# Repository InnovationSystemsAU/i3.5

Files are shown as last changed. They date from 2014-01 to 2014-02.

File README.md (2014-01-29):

i3-ImprovedPP
=============

Prusa i3 Improved ++ For Lasercut

A modified Prusa Iteration 3 printer, designed to have a rigid lasercut frame.

Our modifications include simplification, improvements to the frame, reliability improvements and have optimised the design for next generation
concepts such as direct drive, hall effect sensors and more to come.

Build images can be seen here -

https://imgur.com/a/1nFgI#0

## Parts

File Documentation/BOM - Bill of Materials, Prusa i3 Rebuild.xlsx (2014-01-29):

Revision History
Issue | Release date | Prepared by |  | Reviewed by | Approved by
A |  | M.Croucher
Project Title: | Prusa i3 Improved ++
Notes: | 1. All costs are excluding GST
Line Item | Sub Assembly | Part Number | Issue | Description | Qty/Unit | Supplier | Ordered | Cost per Item | Cost Total
1 | Laser Cut Parts | Prusa_i3_Frame_V2_Laser_Cut_Layout.dxf |  | Frame, Main | 1 |  |  |  | $0.00
2 |  |  |  | Upright, Main Frame | 2 |  |  |  | $0.00
3 |  |  |  | Mount, z-axis Motor | 2 |  |  |  | $0.00
4 |  |  |  | Support, z-axis Motor Mount | 4 |  |  |  | $0.00
5 |  |  |  | Support, z-axis Guide Support | 2 |  |  |  | $0.00
7 | Printed Parts |  |  |  |  |  |  |  | $0.00
8 |  | i3 Improved ++ 1x Y Corner.stl |  | y-Corners | 4 |  |  |  | $0.00
9 |  | i3 Improved ++ X Carriage HD.stl |  | x-Carriage, Heavy Duty | 1 |  |  |  | $0.00
10 |  | i3 Improved ++ X Carriage SD.stl |  | x-Carriage, Standard Duty | 1 |  |  |  | $0.00
11 |  | i3 Improved ++ X Idler End.stl |  | x-axis, Idler End | 1 |  |  |  | $0.00
12 |  | i3 Improved ++ X Motor End.stl |  | x-axis, Motor End | 1 |  |  |  | $0.00
13 |  | i3 Improved ++ Y Belt Clamp.stl |  | y-Carriage, Belt Clamp | 1 |  |  |  | $0.00
14 |  | i3 Improved ++ Y Idler End 8mm.stl |  | y-Carriage, Idler End | 1 |  |  |  | $0.00
15 |  | i3 Improved ++ Y Carriage LM8UU Holder.stl |  | y-Carriage, Bearing Holder | 3 |  |  |  | $0.00
16 |  | i3 Improved ++ Y Motor Mount.stl |  | Mount, y-Motor, w/end stop | 1 |  |  |  | $0.00
17 |  | i3 Logo 30mm Fan Guard.stl |  | Guard, fan 30mm | 1 |  |  |  | $0.00
18 |  | i3 Logo 40mm Fan Guard.stl |  | Guard, fan 40mm | 1 |  |  |  | $0.00
19 |  | 608pulley.stl |  | Pulley, 608 | 2 |  |  |  | $0.00
20 |  | Generic 40mm Fan Mounted LED Strip.stl |  | Strip, Fan Mounted LED strip | 2 |  |  |  | $0.00
21.35087719 |  | i3_improved__x_rod_stabiliser.stl |  | Stabiliser, y-axis Rod | 2 |  |  |  | $0.00
22.4122807 | Direct Drive Extruder |  |  |  |  |  |  |  | $0.00
23.47368421 | Groove Mount | i3 Improved ++ Direct Drive Extruder Mount.stl |  | Mount, Direct Drive Extruder | 1 |  |  |  | $0.00
24.53508772 |  | i3 Improved ++ Direct Drive Extruder Mount.stl |  | Mount, 40mm Fan | 1 |  |  |  | $0.00
25.59649123 |  |  |  |  |  |  |  |  | $0.00
26.65789474 | Budaschnozzle Mount | i3 Improved ++ Buddasch Extruder Mount.stl |  | Mount, Budasch Extruder | 1 |  |  |  | $0.00
27.71929825 |  |  |  |  |  |  |  |  | $0.00
28.78070175 | Ubis Mount |  |  |  |  |  |  |  | $0.00
29.84210526 |  |  |  |  |  |  |  |  | $0.00
30.90350877 |  |  |  |  |  |  |  |  | $0.00
31.96491228 |  |  |  |  |  |  |  |  | $0.00
33.02631579 |  |  |  |  |  |  |  |  | $0.00
34.0877193 | Rod |  |  | Threaded Rod - M8 Stainless Steel, 210mm LG | 3 |  |  |  | $0.00 | M8 Total: | 1790
35.14912281 |  |  |  | Threaded Rod - M8 Stainless Steel, 280mm LG | 1 |  |  |  | $0.00
36.21052632 |  |  |  | Threaded Rod - M8 Stainless Steel, 440mm LG | 2 |  |  |  | $0.00
37.27192982 |  |  |  | Threaded Rod - M5 Stainless Steel 306 300mm LG | 2 |  |  |  | $0.00 | M5 Total: | 600
38.33333333 |  |  |  | Ground Rod, Chrome, Hardened, Æ8mm 405mm LG | 2 |  |  |  | $0.00 | 8mm Rod Total: | 1510
39.39473684 |  |  |  | Ground Rod, Chrome, Hardened, Æ8mm 350mm LG Max | 2 |  |  |  | $0.00
40.45614035 | Fasteners |  |  |  |  |  |  |  | $0.00
41.51754386 | Screws | Motor Screws |  | M3 x 10 LG Socket Head Cap Screw | 15 | Fastener Express (http://www.fastener-express.com/) |  |  | $0.00
42.57894737 |  | Chassis Screws |  | M3 x 15 LG Socket Head Cap Screw | 24 |  |  |  | $0.00
43.64035088 |  |  |  | M3 x 20 LG Socket Head Cap Screw | 8 |  |  |  | $0.00
44.70175439 |  | M4 Tension Screw |  | M4 x 20 LG Socket Head Cap Screw | 1 |  |  |  | $0.00
45.76315789 |  | Pulley Screws |  | M8 x 20 LG Socket Head Cap Screw | 2 |  |  |  | $0.00
46.8245614 | Nuts |  |  | M3 Nut | 18 |  |  |  | $0.00
47.88596491 |  |  |  | M3 Lock Nut | 18 |  |  |  | $0.00
48.94736842 |  | y-belt tension nut |  | M4 Lock Nut | 1 |  |  |  | $0.00
50.00877193 |  | z-axis leadscrew nuts |  | M5 Brass Nut (or Zinc Plate, Not Stainless) | 2 |  |  |  | $0.00
51.07017544 |  |  |  | M8 Nut, Stainless | 22 |  |  |  | $0.00
52.13157895 |  |  |  | M8 Lock Nut, Stainless | 14 |  |  |  | $0.00
53.19298246 | Washers |  |  | M3 Washer | 43 |  |  |  | $0.00
54.25438596 |  |  |  | M8 Washer | 22 |  |  |  | $0.00
55.31578947 | Spring Washers |  |  | M3 Wave/Conical washer | 18 |  |  |  | $0.00
56.37719298 |  |  |  | M8 Spring Washer/Conical washer | 26 |  |  |  | $0.00
57.43859649 | Vitamins |  |  |  |  |  |  |  | $0.00
58.5 |  | Upright Support Brackets |  | Brackets - Bunnings 60x60mm | 2 |  |  |  | $0.00
59.56140351 |  | Y-Belt |  | GT-2 725 LG | 1 | Bilby CNC | Y | $4.00 | $4.00 | Total Ln: | 1570
60.62280702 |  | X-Belt |  | GT-2 845 LG | 1 | Bilby CNC | Y | $4.00 | $4.00
61.68421053 |  | Belt Pulleys |  | GT-2 Pulleys, 16 Teeth, Twin Flange | 2 | Bilby CNC | Y | $5.40 | $10.80
62.74561404 |  |  |  | Bearing, LM8UU Linear (8 for Heavy, 7 for Std) | 8 | Bilby CNC | Y | $1.25 | $10.00
63.80701754 |  |  |  | Bearing, 608Z | 2 | Bilby CNC | Y | $1.50 | $3.00
64.86842105 |  | Extruder |  | Bearing, 624ZZ | 1 | Bilby CNC | Y | $1.20 | $1.20
65.92982456 |  |  |  | Small Cable Ties | 10 |  |  |  | $0.00
66.99122807 |  |  |  | Fan, 40mm, 12VDC | 1 | Bilby CNC | Y | $2.95 | $2.95
68.05263158 |  |  |  | Fan, 30mm, 12VDC | 1 |  |  |  | $0.00
69.11403509 |  |  |  | NEMA 17 Motors | 5 |  |  |  | $0.00
70.1754386 |  |  |  | Coupler, Flexible 5mm to 5mm | 2 | Bilby CNC | Y | $5.45 | $10.90
71.23684211 |  |  |  | Hall Effect Endstop, z-axis | 1 | Bilby CNC | Y | $17.95 | $17.95
72.29824561 |  |  |  | Electronics, |  |  |  |  | $0.00
73.35964912 |  |  |  | Cables |  |  |  |  | $0.00
74.42105263 |  |  |  | LED Strip |  |  |  |  | $0.00
75.48245614 |  |  |  | Build Platform |  |  |  |  | $0.00
76.54385965 |  |  |  | 3D Printing Cream Tape, 48mm wide x 50mm LG | 1 | Bilby CNC | Y | $19.95 | $19.95
77.60526316 | Hot End |  |  |  |  |  |  |  | $0.00
78.66666667 |  |  |  | Brass Barrel, M6 x 40 LG, 1.75 ID | 1 | Bilby CNC | Y | $8.95 | $8.95
79.72807018 |  |  |  | Teflon Tube for Barrel Conversion | 1 | Bilby CNC | Y | $5.45 | $5.45
80.78947368 |  |  |  | Ceramic Insulation Tape | 1 | Bilby CNC | Y | $2.50 | $2.50
81.85087719
82.9122807
83.97368421
85.03508772
86.09649123
87.15789474
88.21929825

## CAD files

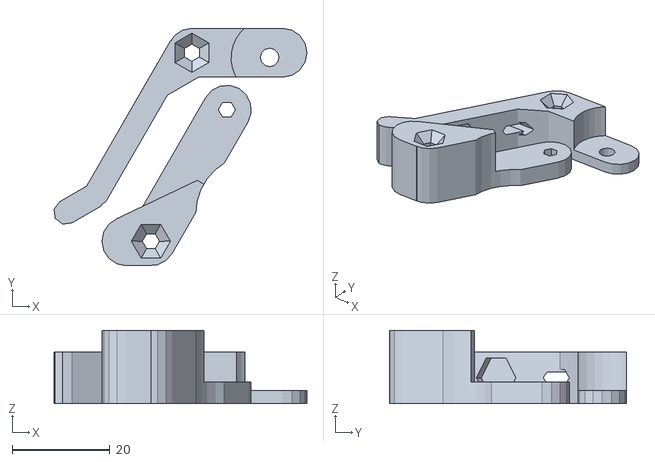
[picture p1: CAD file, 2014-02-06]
i3 Improved ++ Extruder Idler Assembly.stl
51.6 x 48.5 x 15.0

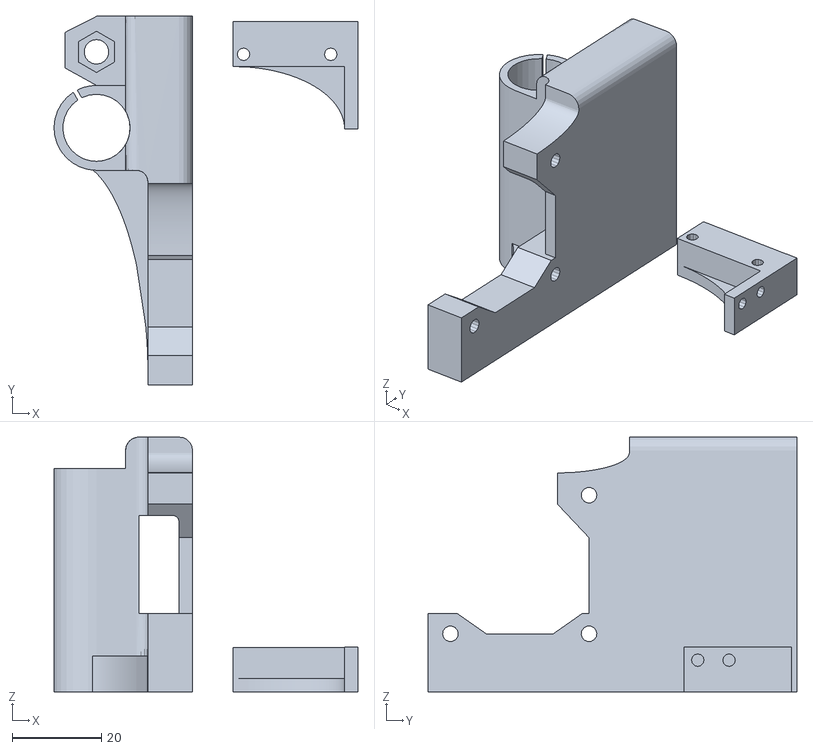
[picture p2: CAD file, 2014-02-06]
i3 Improved ++ X Motor End Assembly.stl
68.0 x 82.5 x 57.0

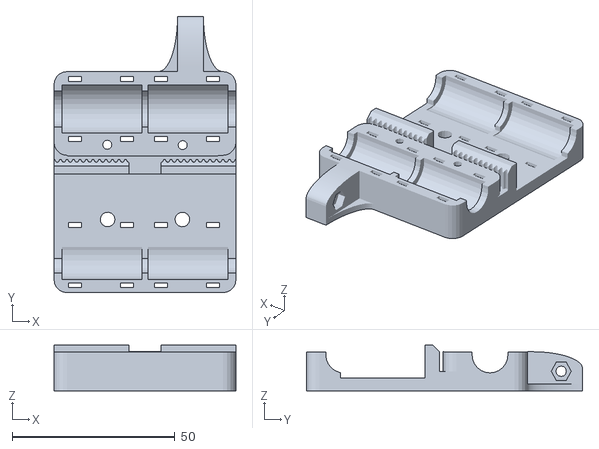
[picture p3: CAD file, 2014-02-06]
i3 Improved ++ X Carriage.stl
56.0 x 85.0 x 14.0

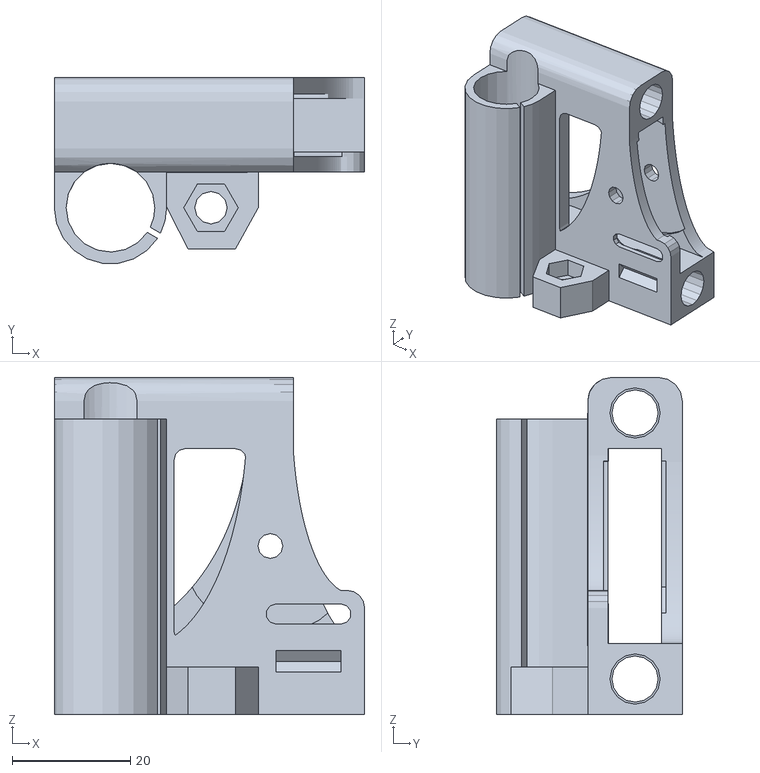
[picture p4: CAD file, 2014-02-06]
i3 Improved ++ X Idler End.stl
52.5 x 31.4 x 57.0

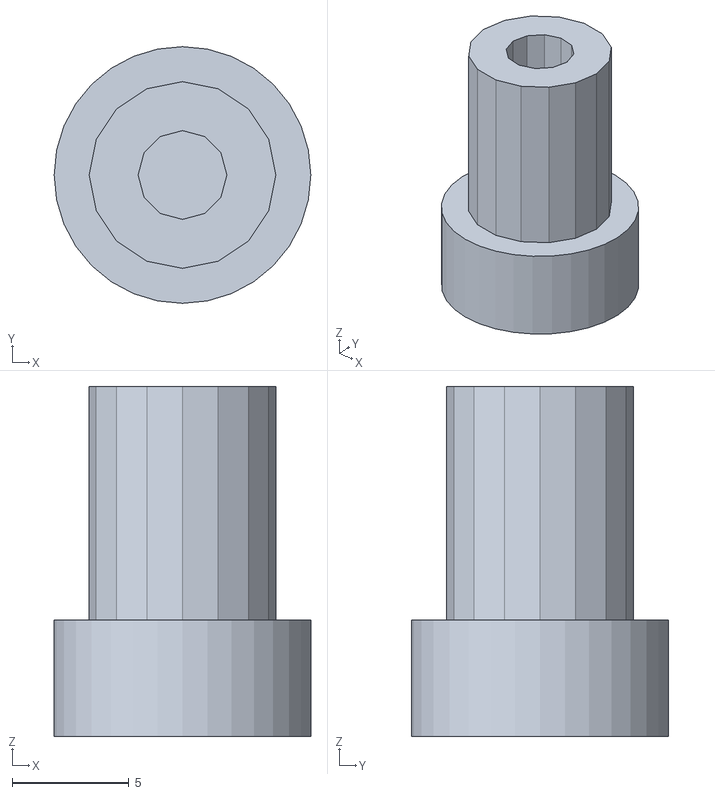
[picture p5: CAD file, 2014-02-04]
i3 Improved ++ Z End Stop Hall Effect Probe.stl
11.0 x 11.0 x 15.0

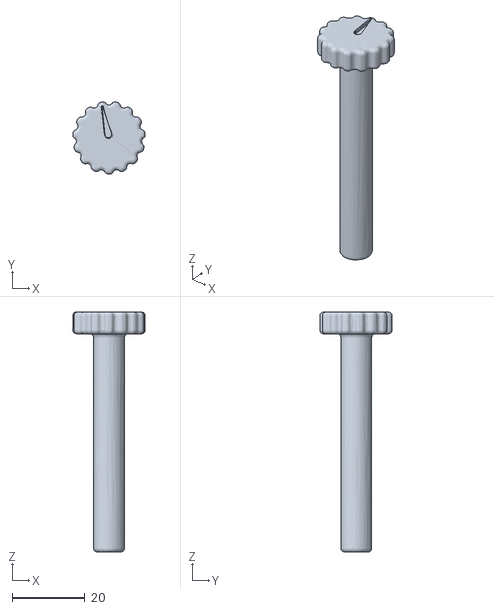
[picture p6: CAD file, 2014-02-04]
i3 Improved ++ Z End Stop Adjustment Dial.stl
19.9 x 19.8 x 66.0

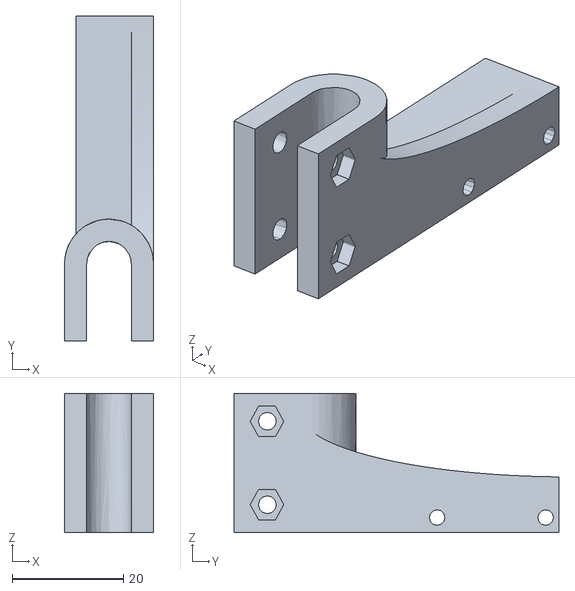
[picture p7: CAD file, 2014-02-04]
i3 Improved ++ Z End Stop Mount.stl
16.0 x 58.4 x 25.0

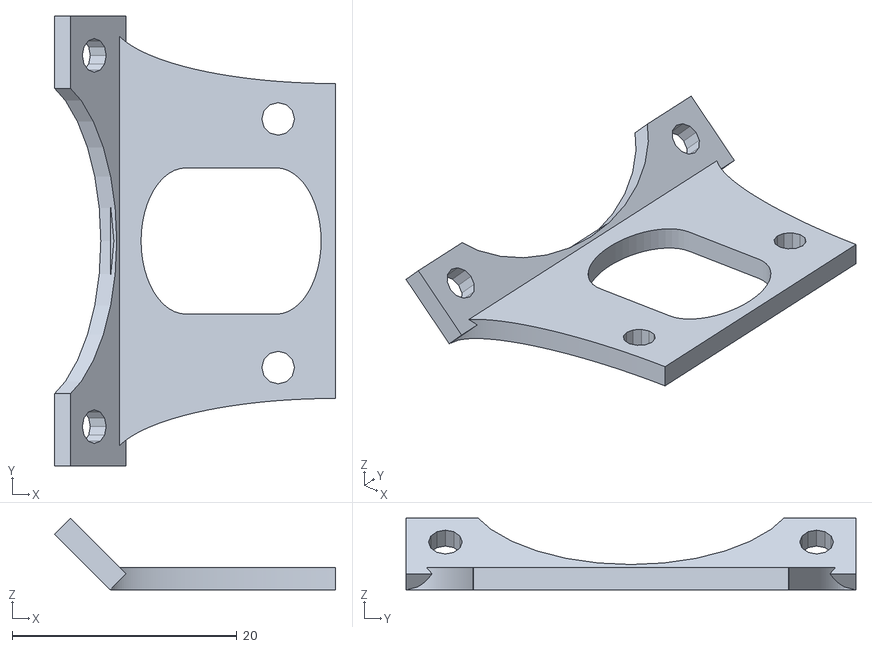
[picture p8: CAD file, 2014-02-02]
i3 Improved ++ Extruder Mount 45 degree Fan Mount.stl
25.0 x 40.0 x 6.36

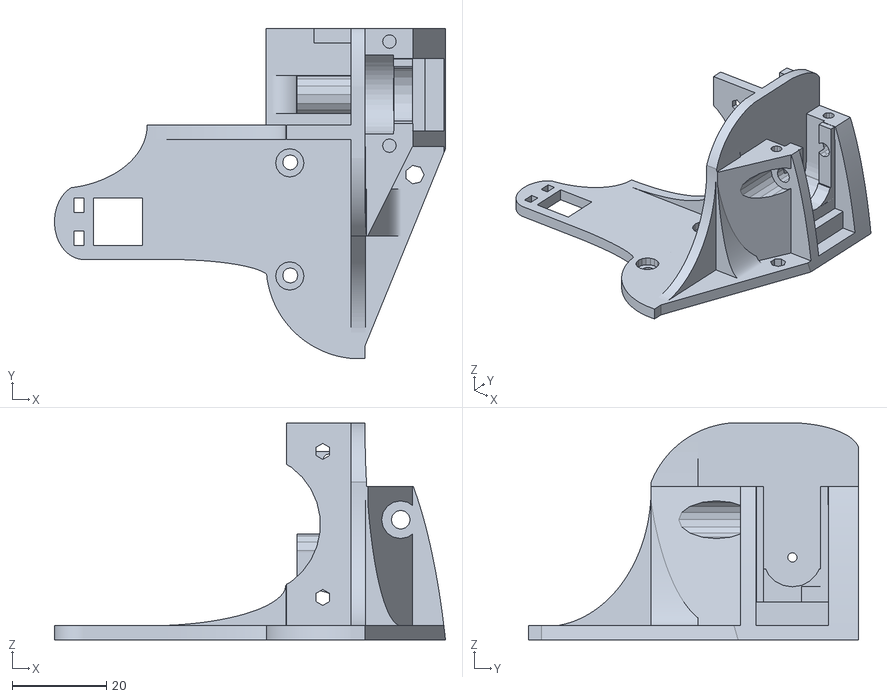
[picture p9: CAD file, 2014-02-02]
i3 Improved ++ Extruder Mount Groove Style.stl
83.0 x 70.0 x 46.0

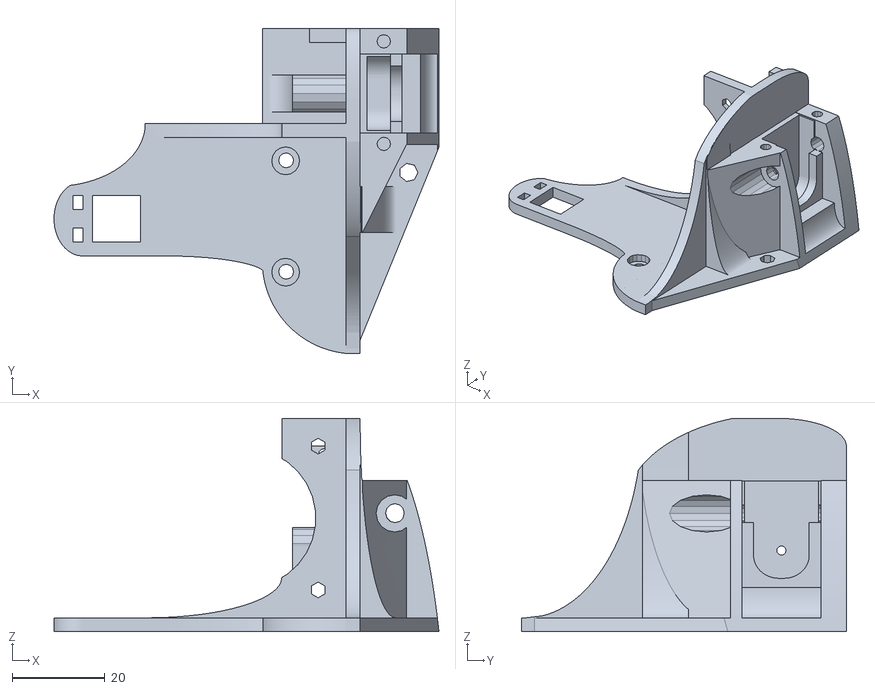
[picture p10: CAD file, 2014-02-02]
i3 Improved ++ Extruder Mount UBIS Style.stl
83.0 x 70.0 x 46.0

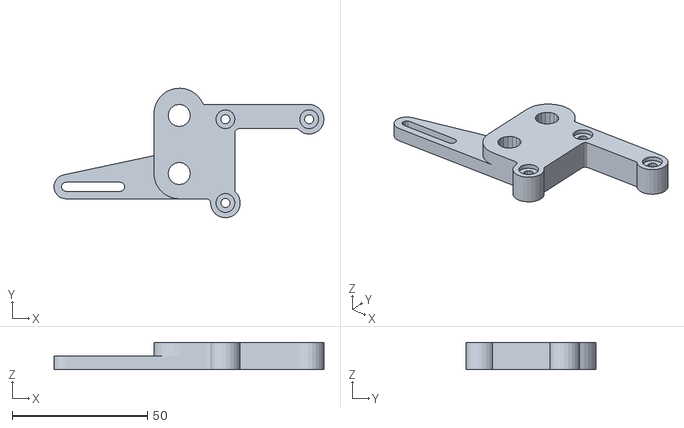
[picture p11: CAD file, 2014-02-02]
i3 Improved ++ Y Motor Mount.stl
100.0 x 48.0 x 10.0

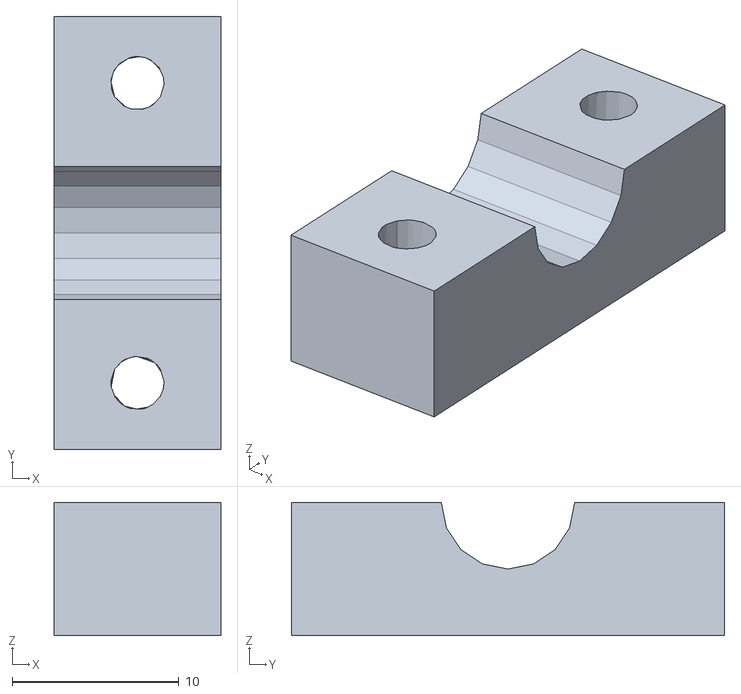
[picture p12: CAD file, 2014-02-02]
i3 Improved ++ Y Brace Clamp.stl
10.0 x 26.0 x 8.00

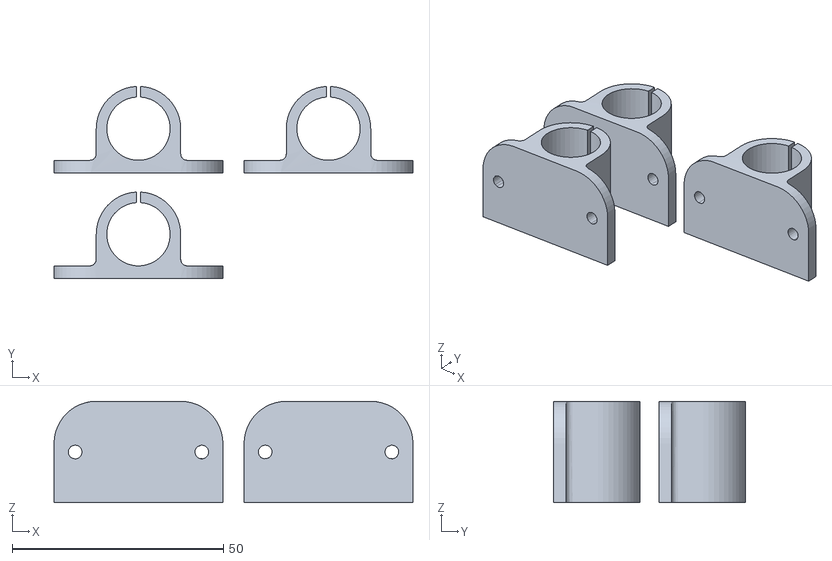
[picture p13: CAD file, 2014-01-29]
i3 Improved ++ Y Bearing Holder.stl
85.0 x 45.5 x 24.0

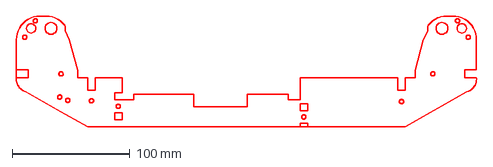
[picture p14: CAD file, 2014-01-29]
i3 Improved ++ HD Top Frame Support.dxf
390.3 x 94.0 mm

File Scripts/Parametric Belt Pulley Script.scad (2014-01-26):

use <hardware.scad>;

bearingsize = 13.3;	//outer diameter of bearings in mm
bearingwidth = 4.8;	//width of bearings in mm
bearingclampsize = 0.5;
bearingclamps = 3;
bearingclampangle = 60;
pulleythick = 1.2;
pulleyflangesize = 1.5;
beltwidth = 6.3;

$fn = 30;

module beltpulley() {
	difference() {
		union() {
			translate([0, 0, pulleythick / 2]) cylinder(h = pulleythick, r = bearingsize / 2 + pulleyflangesize + pulleythick, center = true);
			translate([0, 0, pulleythick + beltwidth + pulleyflangesize / 2]) cylinder(h = pulleyflangesize, r2 = bearingsize / 2 + pulleyflangesize + pulleythick, r1 = bearingsize / 2 + pulleythick, center = true);
			translate([0, 0, pulleythick + beltwidth / 2]) cylinder(h = pulleythick * 2 + beltwidth, r = bearingsize / 2 + pulleythick, center = true);
		}
		translate([0, 0, pulleythick * 1.5 + beltwidth / 2 + pulleyflangesize / 2]) cylinder(h = beltwidth + pulleythick + pulleyflangesize, r = bearingsize / 2, center = true);
		translate([0, 0, pulleythick + beltwidth + pulleyflangesize / 2 + 0.1]) cylinder(h = pulleyflangesize, r1 = bearingsize / 2 - pulleythick, r2 = bearingsize / 2 - pulleythick + pulleyflangesize, center = true);
		translate([0, 0, pulleythick / 2 + beltwidth / 2 + pulleyflangesize / 2]) cylinder(h = beltwidth + pulleythick * 2 + pulleyflangesize, r = bearingsize / 2 - bearingclampsize, center = true);
	}
	difference() {
		translate([0, 0, pulleythick + bearingclampsize + bearingwidth / 2]) cylinder(h = bearingclampsize * 2 + bearingwidth, r = bearingsize / 2 + pulleythick, center = true);
		translate([0, 0, pulleythick / 2 + bearingwidth / 2 + bearingclampsize]) cylinder(h = bearingwidth + pulleythick * 2 + bearingclampsize * 2, r = bearingsize / 2 - bearingclampsize, center = true);
		translate([0, 0, pulleythick + bearingwidth / 2]) cylinder(h = bearingwidth, r = bearingsize / 2, center = true);
		translate([0, 0, pulleythick + bearingwidth + bearingclampsize + bearingclampsize / 2 + 0.1]) cylinder(h = bearingclampsize, r1 = bearingsize / 2 - bearingclampsize, r2 = bearingsize / 2, center = true);
		translate([0, 0, pulleythick + bearingwidth + bearingclampsize / 2 - 0.1]) cylinder(h = bearingclampsize, r1 = bearingsize / 2, r2 = bearingsize / 2 - bearingclampsize, center = true);
		for (angle = [1:bearingclamps]) rotate([0, 0, 360 / bearingclamps * angle]) intersection() {
			translate([0, -bearingsize / 4 - pulleythick / 2, pulleythick + bearingclampsize + bearingwidth / 2]) cube([bearingsize + pulleythick * 2, bearingsize / 2 + pulleythick, bearingclampsize * 2 + bearingwidth + 0.1], center = true);
			rotate([0, 0, 360 / bearingclamps - bearingclampangle]) translate([0, bearingsize / 4 + pulleythick / 2, pulleythick + bearingclampsize + bearingwidth / 2]) cube([bearingsize + pulleythick * 2, bearingsize / 2 + pulleythick, bearingclampsize * 2 + bearingwidth + 0.1], center = true);
		}
	}
}

difference() {
	beltpulley();
	//cube([10, 10, 30]);
}
*%translate([0, 0, pulleythick + bearingwidth / 2]) bearing();

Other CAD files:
i3 Improved ++ Y Belt Clamp.stl
i3_improved__x_rod_stabiliser.stl
i3 Improved ++ Bed Cable Strain Relief.stl
i3 Improved ++ Y Rod Stabiliser.stl
608_idler_spacers.stl
624pulley.stl
Generic 40mm Fan Mounted LED Strip.stl
Generic End Stop Holder.stl
Obsolete/608_idler_spacers.stl
Obsolete/624pulley.stl
Prusa_i3_Frame_V2_Laser_Cut_Layout.DXF
i3 Improved ++ 1 x Y Corner.stl
i3 Improved ++ 4 x Y Corner.stl
i3 Improved ++ 608 Bearing Pulley.stl
i3 Improved ++ Direct Drive Extruder Mount.stl
i3 Improved ++ Extruder Mount Buddasch Style.stl
i3 Improved ++ Standard Endstop Mount.stl
i3 Improved ++ Y Carriage Idler.stl
i3 Improved ++ Z End Stop Adjustment Screw Mount.stl
i3 Logo 30mm Fan Guard.stl
i3 Logo 40mm Fan Guard.STL

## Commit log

2014-01-26 Initial Commit
    Initial Commit, not complete
    [608_idler_spacers.stl, 608pulley.stl, 624pulley.stl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]
2014-01-26 Added new parts
    Added heated bed cable strain relief
    Added X threaded rod stabilisers
    [Prusa_i3_Bed_Cable_Guide.stl, i3_improved__x_rod_stabiliser.stl]
2014-01-27 9mm frame
    9mm frame from thingiverse, made to be cut on small laser cutter.
    Currently no plastic parts or any accessories to fit, just added as
    potential idea for additional rigidity. Maybe a 6mm/9mm hybrid could be
    good?
2014-01-27 Changed Y Idler End
    Replaced old version of Y idler with Matt's suggestion to go for a
    straight 8mm bolt. Hole simply made larger to accomodate.
    [i3 Improved ++ Y Carriage Idler.stl, i3 Improved ++ Y Idler End 8mm.stl]
2014-01-27 Chaned X Idler End
    Changed the X idler end to have hole suitable for M8 bole as per Matt's
    suggestion.
    [i3 Improved ++ X Idler End.stl]
2014-01-29 Changed belt clamp holes
    Made zip tie holes in belt clamp larger as the original ones were a
    shade too small. Zip ties now fit snugly.
    [i3 Improved ++ Y Belt Clamp.stl, i3 Improved ++ Y Carriage Belt Clamp.stl]
2014-01-29 BOM, Prusa i3 Improved ++
    Draft BOM for the Prusa i3 Improved ++
    [BOM - Bill of Materials, Prusa i3 Rebuild.xlsx]
2014-01-29 Added better top frame support
    Better top frame support borrowed from the makerfarm design. Should
    correct lateral flex issue.
    [i3 Improved ++ HD Top Frame Support.dxf]
2014-01-29 File Name Cleanup
    Did a clean up of file names and moved some older parts to a new folder
    to get them out of the production area.
    [608_idler_spacers.stl, 624pulley.stl, Generic End Stop Holder.stl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]
2014-01-29 Original twelvepro Y carriage bearing holder
    Repaired drawing and reverted to original LM8UU bearing holder for
    better prints. The replacement one had overhang.
    [i3 Improved ++ Y Bearing Holder.stl, i3 Improved ++ Y Carriage LM8UU Holder.stl]
2014-01-30 Fixed minor drawing issues
    Fixed some minor drawing issues. The idler end had a spoggy on the
    inside of the bearing tube, which is now cleared and the motor end had
    10mm holes for the threaded rod, now changed to 8mm.
    [i3 Improved ++ X Idler End.stl, i3 Improved ++ X Motor End.stl]
2014-01-31 Fixed drawing
    Adjusted rod hole spacing and slightly enlarged rod holes, a shade too
    small to comfortably take the rod
    [i3 Improved ++ Y Motor Mount.stl]
2014-02-02 Did housekeeping and added new parts
    Changed a few file names to make them more rational. Added the grove and
    ubis extruder mounts, now fixed to be able to be made in ABS properly.
    Added the Y brace clamp. Added motor mount corrected for 8mm rods. Added
    fan mount as a single part
    [i3 Improved ++ Extruder Mount 45 degree Fan Mount.stl, i3 Improved ++ Extruder Mount Buddasch Style.stl, i3 Improved ++ Extruder Mount Groove Style.stl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]
2014-02-02 Removed incorrect file
    This file was named incorrectly
    [i3 Improved ++ X Motor End.stl]
2014-02-02 Added correct X motor end drawing
    This is the correct X motor end drawing.
    [i3 Improved ++ X Motor End.stl]
2014-02-04 Added New Z End Stop
    Added the adjustable Z end stop suitable for Hall, opto or mechanical
    switches. Photo here -
    http://i.imgur.com/xr7woHK.jpg
    [i3 Improved ++ Z End Stop Adjustment Dial.stl, i3 Improved ++ Z End Stop Adjustment Screw Mount.stl, i3 Improved ++ Z End Stop Hall Effect Probe.stl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]
2014-02-06 Revert "Changed Y Idler End"
    This reverts commit 1c6c2636e21c3ed518626b194d8c4236f75aa3d7.
    [i3 Improved ++ Y Carriage Idler.stl, i3 Improved ++ Y Idler End 8mm.stl]
2014-02-06 Added X carriage parts and extruder idler
    Added the modified X carriage parts to take end stops and the 624
    bearing pulley for better belt run. You can still put a 608 on there but
    the belt run is bad. Also discontinued the SD carriage, the 4 bearing
    carriage traverses a lot nicer.
    [i3 Improved ++ Extruder Idler Assembly.stl, i3 Improved ++ X Carriage HD.stl, i3 Improved ++ X Carriage SD.stl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]
